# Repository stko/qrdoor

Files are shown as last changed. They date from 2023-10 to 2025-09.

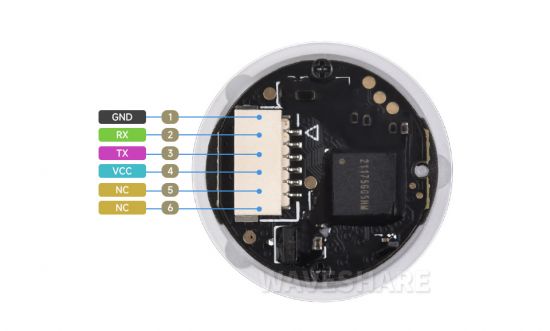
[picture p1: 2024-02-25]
circuit/pico/Barcode_module_b05.jpg

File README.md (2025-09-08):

# QRDoor - A QRCode Reader & MQTT Door Opener

Even as made as add-on for the [Zuul Acess Control System](https://github.com/stko/zuul-ac), it's also suitable whereever a MQTT driven QR code reader and door opener output is needed.

## What it does
* it quickly reads all codes which are presented to the camera
* the read codes are sent as a mqtt message
* it waits for incoming mqtt messages to activate the output pin (to control a door opener)
* as a convinience function, it monitors an input pin (as door bell button) and reports its state change via mqtt

## Setup
For the hardware connect your rpi pico as shown in the circuit/qrcode_pico schematic.

For the software installion the Thonny IDE was used. The steps are
* for micropython follow the instructions on https://micropython.org/download/RPI_PICO_W/. Make sure you install the version for the *WIFI version* of the Rasperry Pico!
* connect your Thonny IDE with your pico device
* In Thonny, in "Tools/Manage Packages.." install the both packages umqtt.simple2 and umqtt.robust2 (MAKE SURE YOU GOT THE ....2 VERSION)
* copy the provided file `settings_template.json`to `settings.json`
* edit the new file `settings.json` and set your own settings
* via Thonny, copy both main.py and settings.json onto your pico device
* run the program

## Operation
* at start qrdoor tries to connect with the given WIFI. This loop is repeated until the connection is made.
* then it waits for either for a scanned code, a button press or an open command

## MQTT commands
### Scanned code
When a code is read, its published to `qrdoor/<device- id>/code`
  
### Button Press
When the button is pressed or released, the state is reported to `qrdoor/<device- id>/button` as `on` or `off`

### Door Open command
When the `qrdoor/<device- id>/open` \<secs\> topic is received, both LED and output pins are set to High for \<secs\> seconds. To avoid unwanted longer power output, this time is limited to 5 secs.

## Setup
Depending on the factory setting of a fresh GM60 qr code reader out of the box, it might be that the qr code reader does not send a trailing <CR> after each scan, which is needed by the software to identify the end of the scan. To fix this, there are configuration QR Codes in the GM60 user manual. Just scan the one named "Add tail 'CR'" to set the trailing <CR>.

## History
Originally the whole project was started to use a ESP32CAM module for it. This work can be found in the qrdoor folder as an Arduino Project. It finally worked in some way, but it came out that the ESPCAM can't handle it properly when suddenly a mobile phone with a qrcode on it is presented to the camera. All the brightness control and auto focus need to be completely re- adjusted, which takes at least 10 seconds, and during the whole time the user needs to hold the mobile phone stable and calm in a constant position and distance in front to the camera - and this just don't work.

So finally the whole project was restarted, this time with a Raspberry Pico, Micropython and the ready-to-go QR-Code Reader from Waveshare (which seems to be a GROW GM861, which can be ordered in Asia). With that it just took a relaxed weekend to get it to work, mainly because of the very well working barcode reader.

## Links

Micropython Image *with* WLAN - Support:  https://micropython.org/download/rp2-pico-w/rp2-pico-w-latest.uf2
The QR Reader Module: https://www.waveshare.com/wiki/Barcode_Scanner_Module_(D)
which is a GROW GM60 module

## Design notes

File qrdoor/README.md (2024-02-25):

# QRDoor - Scans QRCodes via ESP32-CAM and send them via MQTT

(not fully finalized, QR is working, the additional IOs are not implemented yet)

QRDoor is a generic application to read QRCodes with a ESP32-CAM module and forward them via MQTT.

It also supports, controlled by MQTT :
- one Input (e.g. for adoor bell button)
- one triggered output port (for the door lock)

All the Wifi setup is made through the [WifiMQTTManager](https://github.com/dreed47/WifiMQTTManager/tree/master#access-point-configuration), which provides an easy to use setup hotspot.

## Limitations
Please be aware that the combination of cheap processor and low-cost camera is far behind the performance of a Desktop PC with a high speed & resolution webcam. What does that mean in detail?:
* The standard lens together with the auto focus allows only a small distance range where the qrcode can be placed (~25 cm). If it is too far, the qrcode becomes too small, but if it is too close, the picture becomes blurry
* The autofocus and the brightness control is very slow, and each picture change triggers a re-adjustment

Because of that it's quite impossible to just hold a mobile phone free hand anywhere in front of the camera. The movements of the hand are much quicker as the autofocus :-(

So to read a qrcode from any surface or from a phone, it's highly recommended to construct something like a filing for the object carrying the qrcode in front of the camera to keep the object in position so that the camera can generate a stable picture.

Also the user needs to be made aware that the recognition process can easily take 10 seconds...

## Hardware

Just as a starting point the io pins have been taken from [here](https://www.electroniclinic.com/esp32-cam-smart-iot-bell-circuit-diagram-and-programming/) and put into a KiCad schematic separated into two sections:
* one pcb close to the bell transformator containing the DC converter and the door opener output
* a second pcb carrying the ESP32cam and its voltage converter

Schematic

## Setup

The development was made with the VSCode Arduino Extention, so the setup for the original Arduino IDE should be very simular.

1) First add (if not already done) the URL for the Espressif Board in "Board Manager / Addional URLs":“[https://dl.espressif.com/dl/package_esp32_index.json”](https://dl.espressif.com/dl/package_esp32_index.json%E2%80%9D)

2) In the Board Manager, search for "esp32" and install "Esp32 from Espressif Systems”
3) Select the right board: “ESP32 Wrover"
4) In the Library Manager, install several Libraries. Here's the output from the todays build log:

```
Used library            Version     Pfad                                                                             
WiFiMQTTManager Library 1.0.1-beta   
WiFiManager             2.0.15-rc.1            
WiFi                    2.0.0
Update                  2.0.0
WebServer               2.0.0
DNSServer               2.0.0
ArduinoJson             5.13.5
PubSubClient            2.8
FS                      2.0.0
SPIFFS                  2.0.0
```
Make sure the Arduino Json Library  is a **5.xx** version!!

In Tools-Board select :
- ESP32Wrover Module
- Speed 921600
- Flash Frequency 80Mhz
- Flash Mode QIO
- Partition Scheme: Huge app

## Hacks

After installing WiFiMQTTManager, go into the library file `.../WiFiMQTTManager.cpp` and move the `Serial.begin(115200);`line as the first line of the constructor

```WiFiMQTTManager::WiFiMQTTManager(int resetPin, char* APpassword) {
  Serial.begin(115200);
  wm = new WiFiManager;
  lastMsg = 0;
  formatFS = false;
  ```

add the line `client->setBufferSize(512);` after the `client.reset(new PubSubClient(_espClient));`

```
  client.reset(new PubSubClient(_espClient));
  client->setBufferSize(512);
  client->setServer(_mqtt_server, port);
  ```

comment out the line 158 `wm->resetSettings();` to not loose all settings after failed MQTT server attempt.. and modify delay timings

```
  client->setServer(_mqtt_server, port);
  delay(2000);
  Serial.print("WMM: attempting MQTT connection...");
  if (!client->connect(clientId)) {
    Serial.println("failed to connect to MQTT -wait 10 secs and restart...");
    delay(10000);
//    wm->resetSettings();
    ESP.restart(); 
```

Modify the `SPIFFS.begin()` line from

` if (SPIFFS.begin()) {`

to 

 `if (SPIFFS.begin(false) || SPIFFS.begin(true)){ `

to format the filesystem at the inital start

in \~/snap/arduino/85/.arduino15/packages/esp32/hardware/esp32/1.0.6/cores/esp32/main.cpp

increase the task stack size

```cpp
#ifndef CONFIG_ARDUINO_LOOP_STACK_SIZE
#define CONFIG_ARDUINO_LOOP_STACK_SIZE 8192
#endif

//// ---- ADD this -----
#define CONFIG_ARDUINO_LOOP_STACK_SIZE 32768
```

## Credits

- The program skeleton comes from the  WiFiMQTTManager demo code

- The image capture routines are from [GitHub - donny681/ESP32_CAMERA_QR](https://github.com/donny681/ESP32_CAMERA_QR)

-  The qrcode detection routines are from [GitHub - dlbeer/quirc: QR decoder library](https://github.com/dlbeer/quirc)
and

- qrcode code sample [GitHub - donny681/ESP32_CAMERA_QR](https://github.com/donny681/ESP32_CAMERA_QR)

Detailed Info about the ESP32CAM: https://lastminuteengineers.com/getting-started-with-esp32-cam/

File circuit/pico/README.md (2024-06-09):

# Details

## Pico Pinout

top view, QRCode reader on the left, Power on the right

| Left | Right |
| --- | ----- |
| BL | |
| OR | |
| BR | |
| GR | |
| (Relay) | GN |
| (GND) | WH |
| (V+) | RT |

## Power supply

| Meaning | (color) |
| --- | --- |
| AC/DC 1 | |
| AC/DC 2 | |
| Door Opener 1 | |
| Door Opener 2 | |
| V+ | RT |
| GND | WH |
| Relay | GN |

## QRCode- Reader Pinout

GND: Ground
RX: UART input pin
TX: UART output pin
VCC: 3.3V power supply
NC: Reserved, not connected
NC: Reserved, not connected

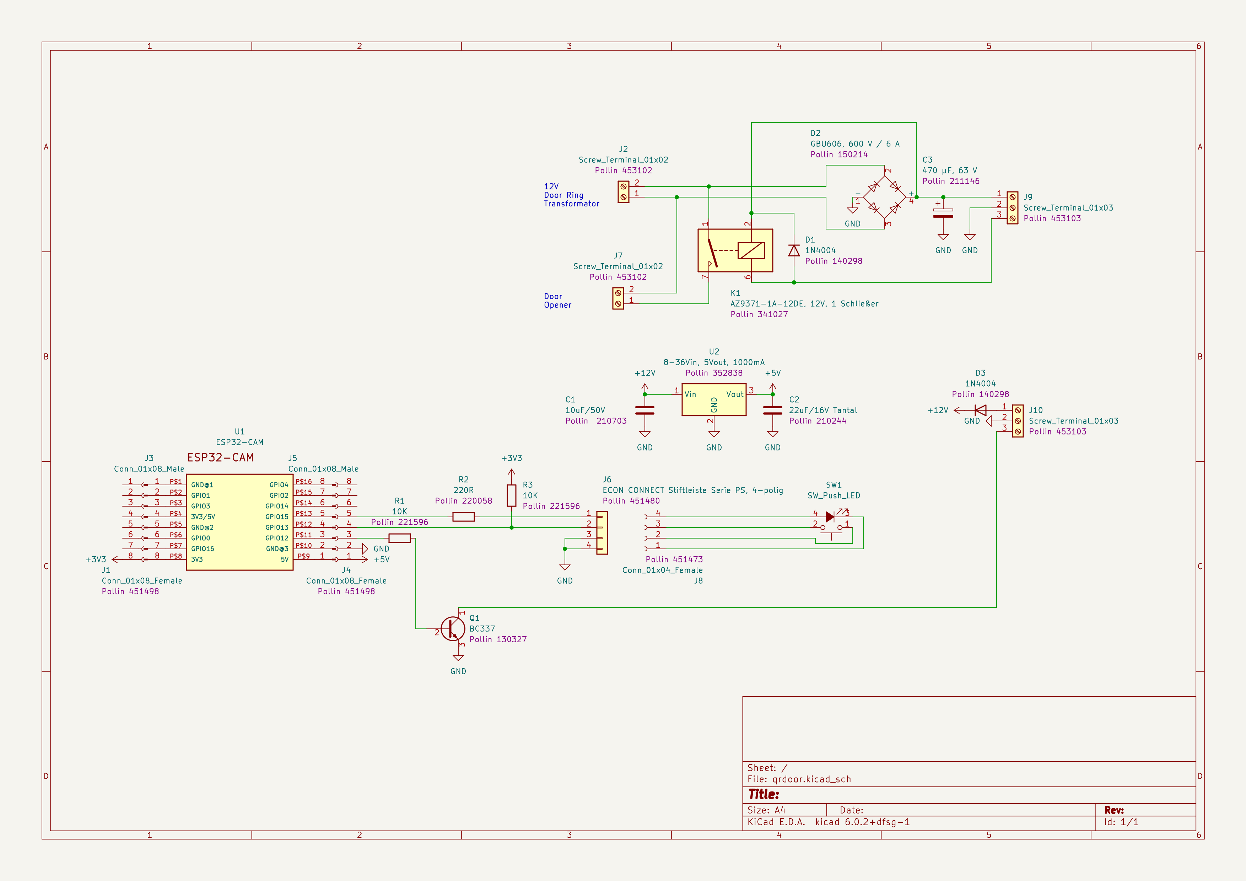
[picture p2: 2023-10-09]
images/schematig.png

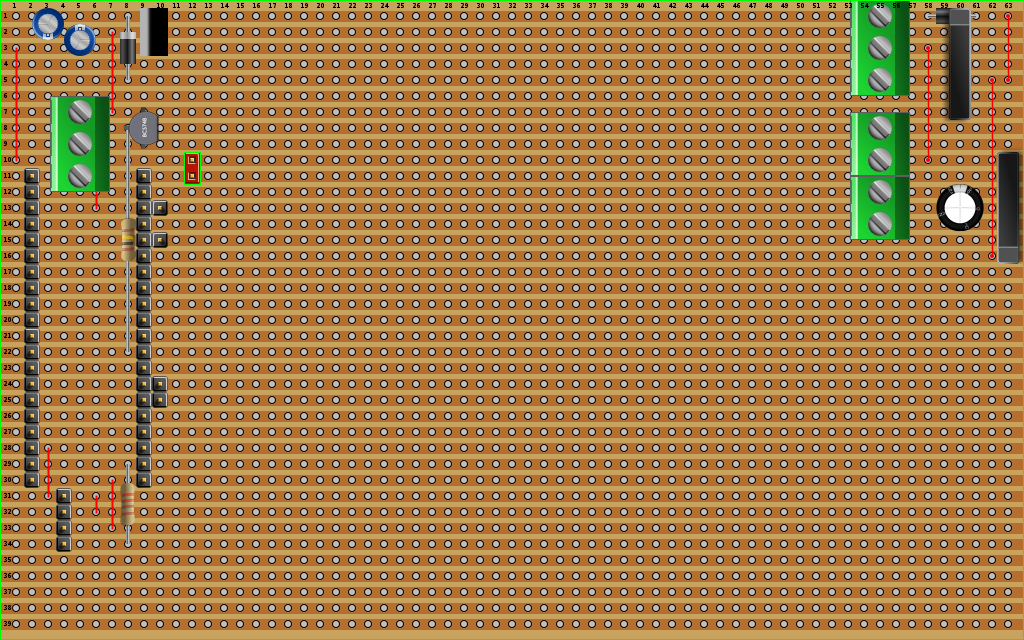
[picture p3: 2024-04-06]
circuit/pico/pcb_cheap.png

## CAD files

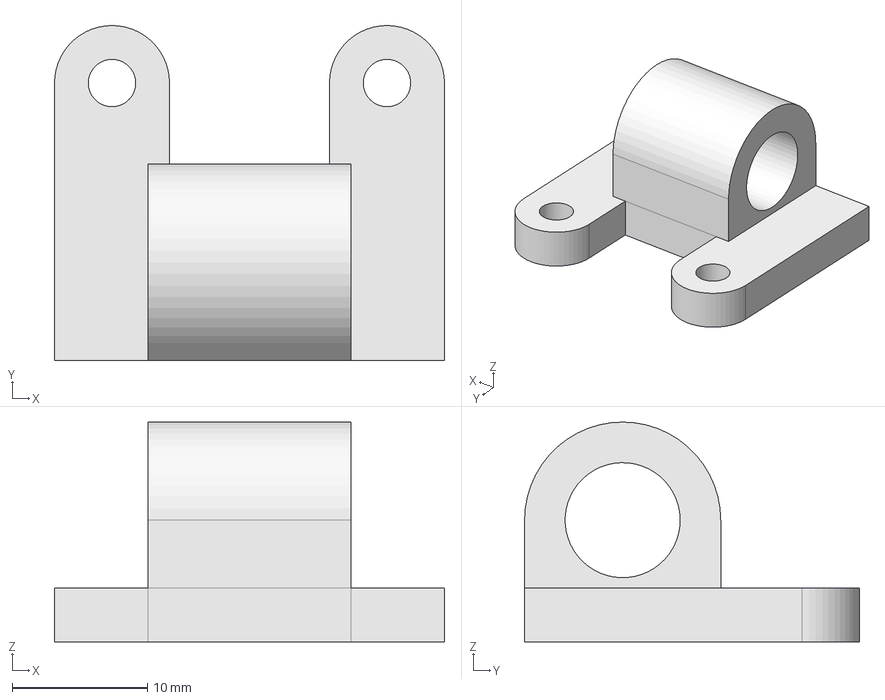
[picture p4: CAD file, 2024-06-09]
cad/pcb_holder_small.FCStd
28.8 x 24.8 x 16.3 mm

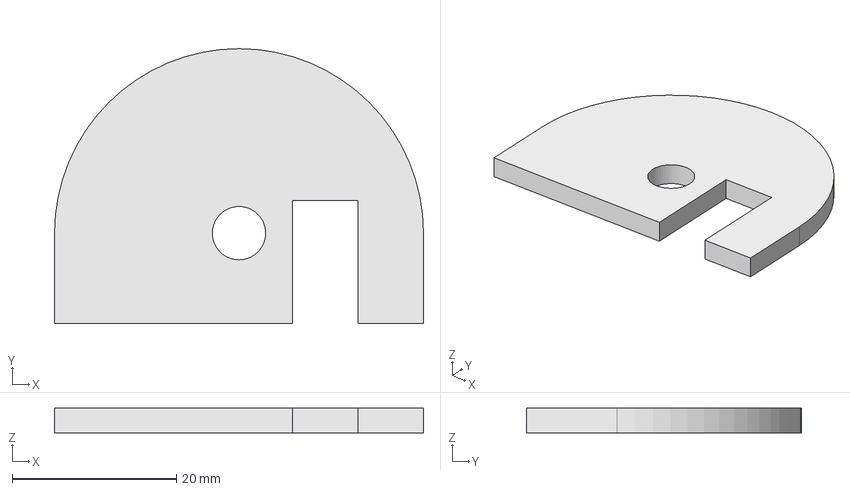
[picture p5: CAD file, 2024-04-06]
cad/front_plate_2_M6.FCStd
45.0 x 33.5 x 3.00 mm

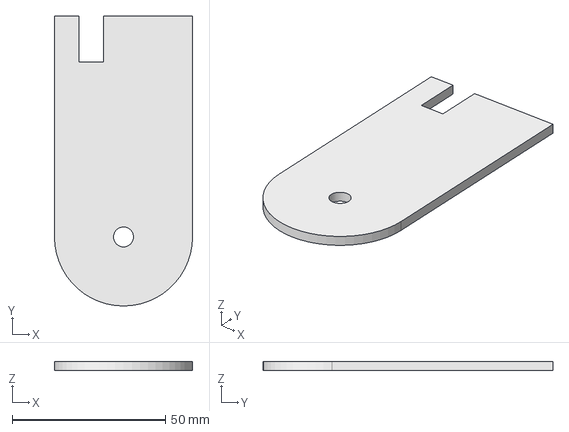
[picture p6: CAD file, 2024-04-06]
cad/front_plate_3_M6.FCStd
45.0 x 94.5 x 3.00 mm

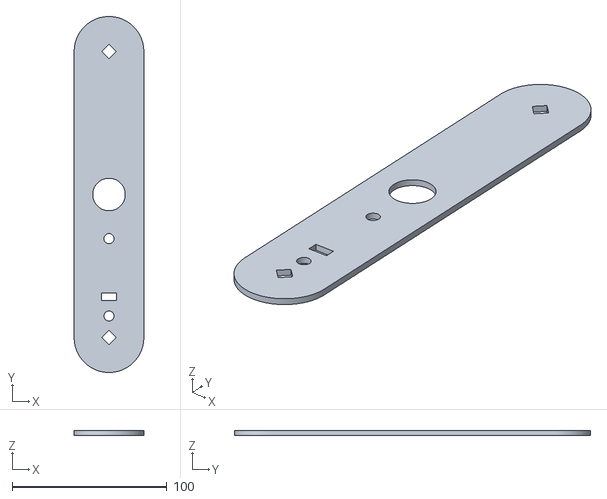
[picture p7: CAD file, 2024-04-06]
cad/front_plate_M6-Körper.stl
45.0 x 230.0 x 3.00

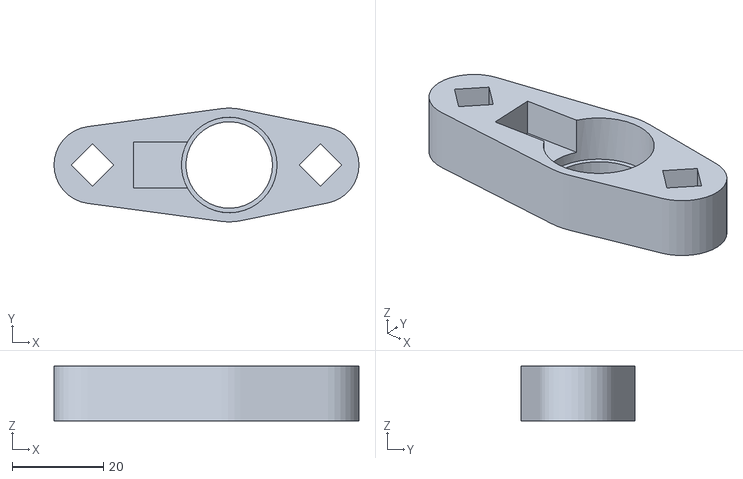
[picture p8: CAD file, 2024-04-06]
cad/camera_cover_M6-Körper.stl
67.0 x 25.0 x 12.0

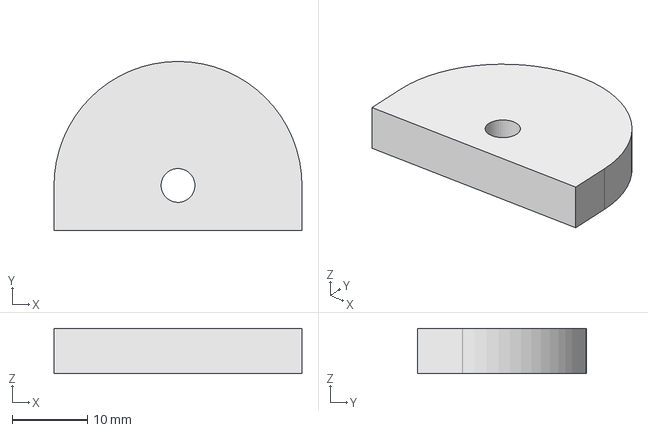
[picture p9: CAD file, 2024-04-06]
cad/distance_plate.FCStd
33.0 x 22.5 x 6.00 mm

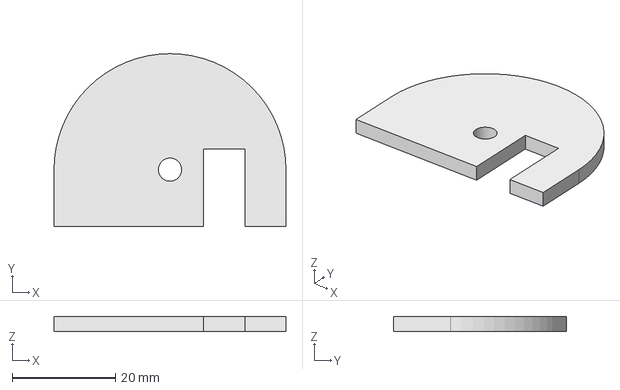
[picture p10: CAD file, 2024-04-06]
cad/front_plate_2.FCStd
45.0 x 33.5 x 3.00 mm

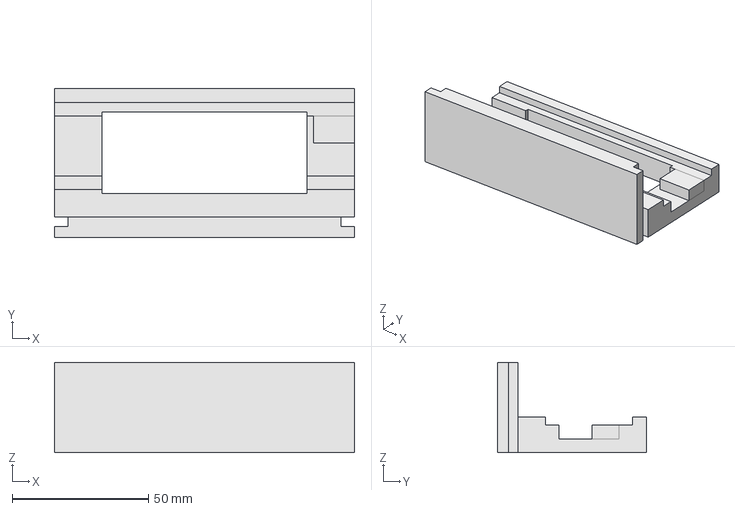
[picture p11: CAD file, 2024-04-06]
cad/pcb_holder.FCStd
110.0 x 54.5 x 33.0 mm

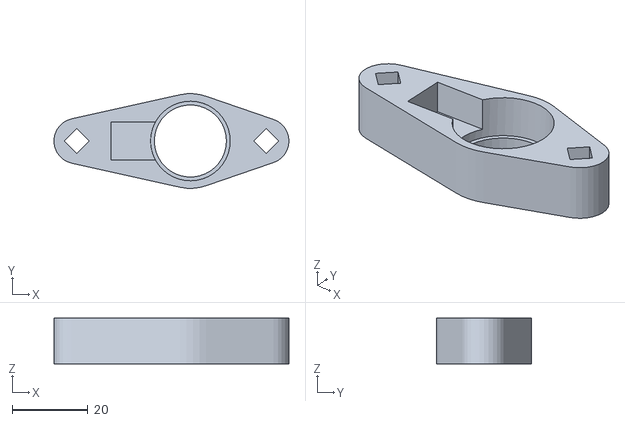
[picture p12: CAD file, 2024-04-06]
cad/camera_cover-Körper.stl
62.0 x 25.0 x 12.0

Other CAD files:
cad/front_plate_2_M6-Körper.stl
cad/pcb_holder-Körper.stl
cad/camera_cover_M6.FCStd
cad/front_plate.FCStd
cad/distance_plate_M6.FCStd
cad/front_plate_3.FCStd
cad/distance_plate_M6-Körper.stl
cad/distance_plate-Körper.stl
cad/front_plate_M6.FCStd
cad/camera_cover.FCStd
cad/front_plate_3_M6-Körper.stl

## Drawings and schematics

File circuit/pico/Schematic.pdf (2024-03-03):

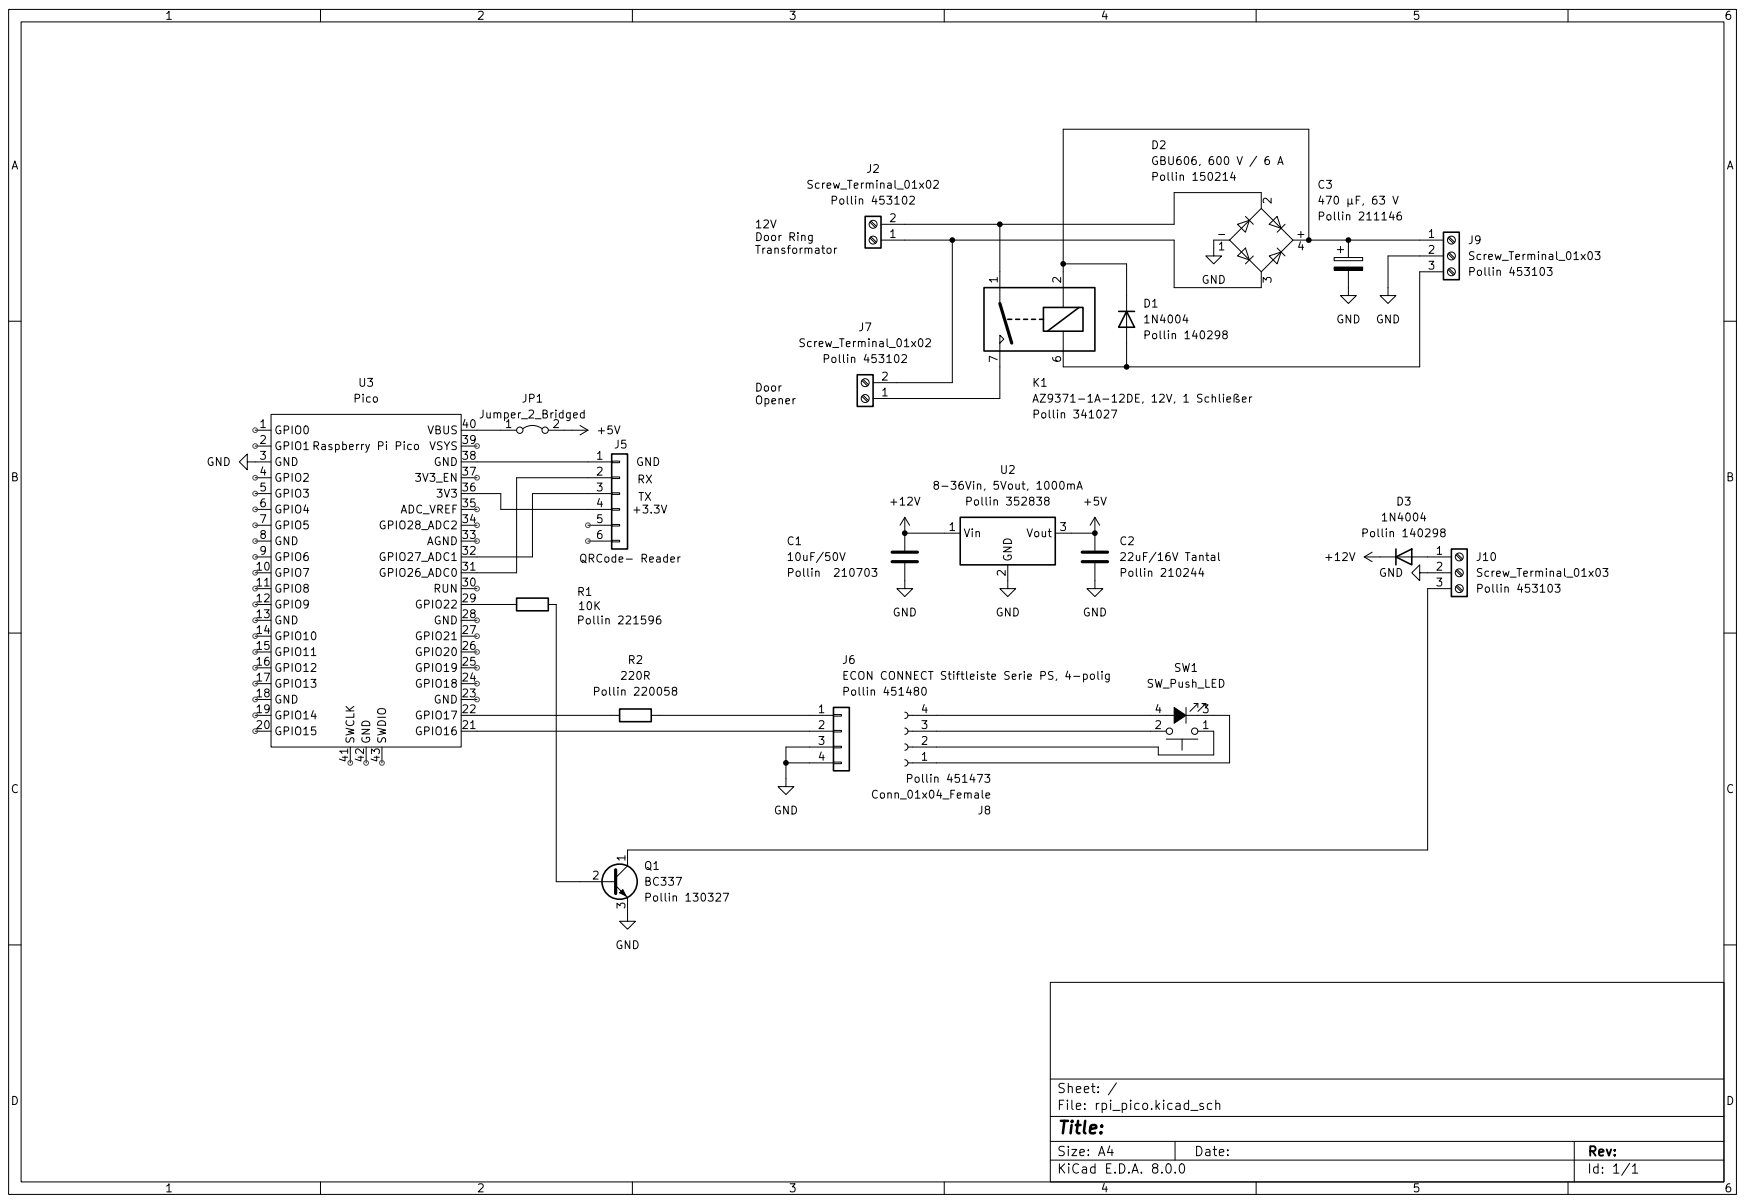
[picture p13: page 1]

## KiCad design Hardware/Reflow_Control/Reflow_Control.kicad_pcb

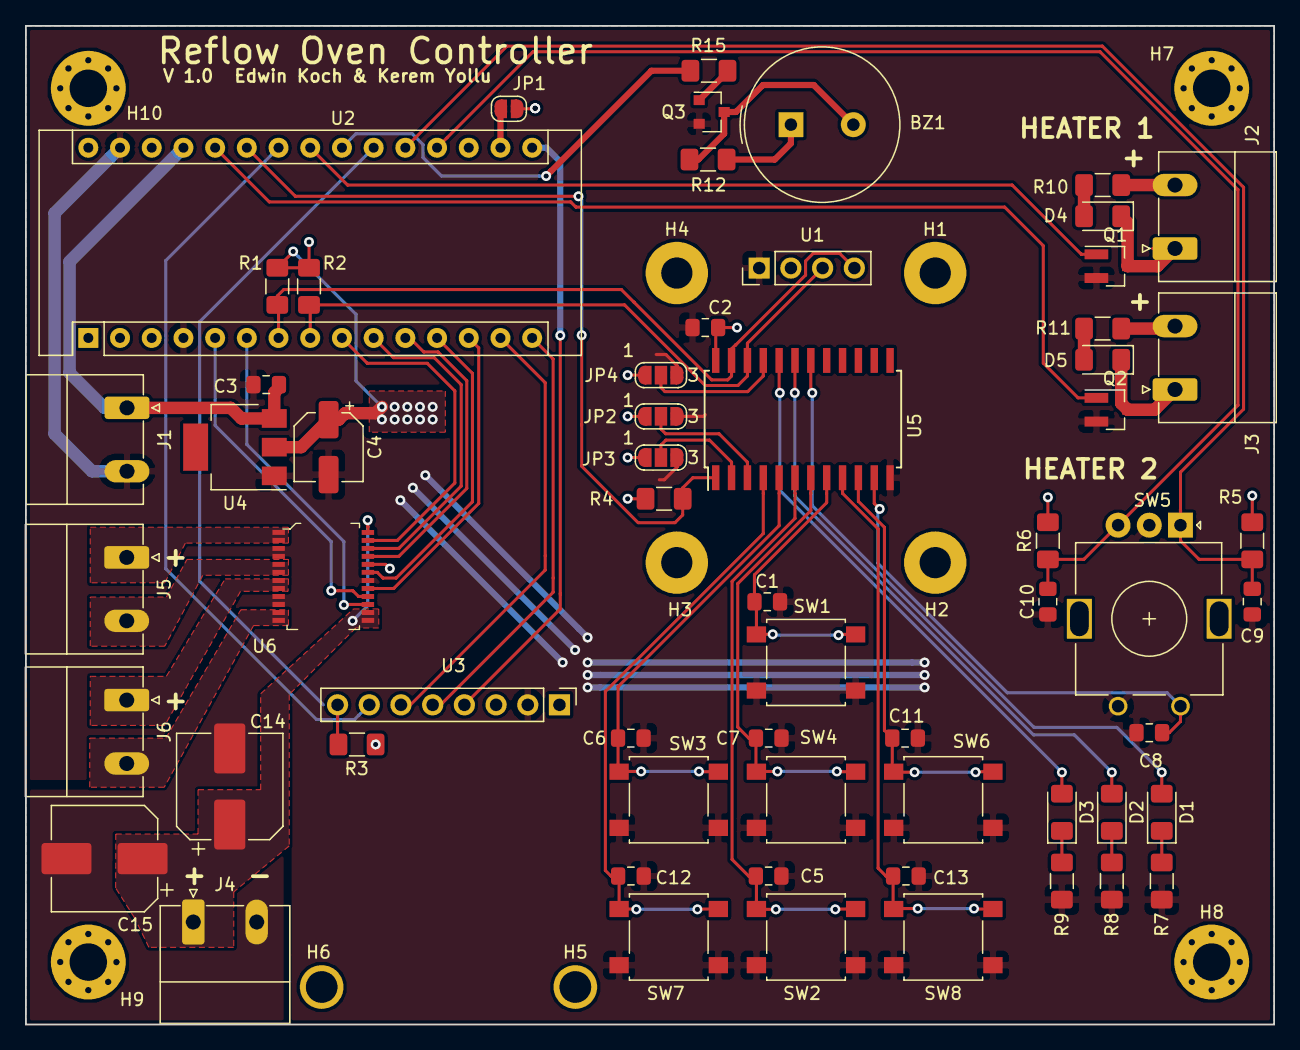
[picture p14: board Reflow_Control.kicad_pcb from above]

Board: 2 copper layers, 100.0 x 80.0 mm, 71 parts (0 on the bottom side), 52 nets.

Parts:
BZ1: Buzzer; Buzzer_TDK_PS1240P02BT_D12.2mm_H6.5mm
C1, C3, C5, C6, C7, C8, C9, C10, C11, C12, C13: 10uF; C_0805_2012Metric_Pad1.15x1.40mm_HandSolder
C2: 100n; C_0805_2012Metric_Pad1.15x1.40mm_HandSolder
C4: 100uF; CP_Elec_5x5.4
C14, C15: 100uF; CP_Elec_8x6.2
D1, D2, D3, D4, D5: LED; LED_1206_3216Metric_Pad1.42x1.75mm_HandSolder
H1, H2, H3, H4, H5, H6: MountingHole; MountingHole_2.5mm_Pad
H7, H8, H9, H10: MountingHole; MountingHole_3mm_Pad_Via
J1: Conn_5V; PhoenixContact_MC_1,5_2-G-5.08_1x02_P5.08mm_Horizontal
J2: Conn_ssr_1; PhoenixContact_MC_1,5_2-G-5.08_1x02_P5.08mm_Horizontal
J3: Conn_ssr_2; PhoenixContact_MC_1,5_2-G-5.08_1x02_P5.08mm_Horizontal
J4: Conn_mot_PWR; PhoenixContact_MC_1,5_2-G-5.08_1x02_P5.08mm_Horizontal
J5: Conn_mot_1; PhoenixContact_MC_1,5_2-G-5.08_1x02_P5.08mm_Horizontal
J6: Conn_mot_2; PhoenixContact_MC_1,5_2-G-5.08_1x02_P5.08mm_Horizontal
JP1: 3.3V Jumper; SolderJumper-2_P1.3mm_Open_RoundedPad1.0x1.5mm
JP2, JP3, JP4: ADDR_A2; SolderJumper-3_P1.3mm_Open_RoundedPad1.0x1.5mm_NumberLabels
Q1: Q_NMOS_GSD; SOT-23_Handsoldering
Q2: NUD3112LT1G; SOT-23_Handsoldering
Q3: BC848; SOT-23
R1, R2, R3, R4, R5, R6, R7, R8, R9: 4k7; R_1206_3216Metric_Pad1.42x1.75mm_HandSolder
R10, R11, R12, R15: 1k; R_1206_3216Metric_Pad1.42x1.75mm_HandSolder
SW1, SW2, SW3, SW4, SW6, SW7, SW8: SW_Push; SW_SPST_B3S-1000
SW5: Rotary_Encoder_Switch; RotaryEncoder_Alps_EC11E_Vertical_H20mm
U1: SSD1306_128x64; PinHeader_1x04_P2.54mm_Vertical
U2: NUCLEO-F042K6; Arduino_Nano
U3: MAX31865_Breakout; PinHeader_1x08_P2.54mm_Vertical
U4: LM1117-3.3; SOT-223
U5: PCA9555; SOIC-24W_7.5x15.4mm_P1.27mm
U6: TB6612FNG_C_8_EL; LSSOP-24_W5.6mm

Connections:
+3V3: BZ1.1, C2.2, C4.1, J2.2, J3.2, JP1.2, JP2.1, JP3.1, JP4.1, R1.1, R2.1, R3.1, R4.1, R5.1, R6.1, R10.1, R11.1, R12.1, U1.2, U3.3, U4.2, U5.24, U6.20
+5V: C3.1, J1.1, U2.27, U4.3
/motor_vcc: C14.1, C15.1, J4.1, U6.13, U6.14, U6.24
ADDR_A0: JP4.2, U5.21
ADDR_A1: JP3.2, U5.2
ADDR_A2: JP2.2, U5.3
BTN_A: C12.1, SW7.1, U5.4
BTN_B: C13.1, SW8.1, U5.9
BTN_CENTER: C7.1, SW4.1, U5.7
BTN_DOWN: C5.1, SW2.1, U5.6
BTN_LEFT: C6.1, SW3.1, U5.5
BTN_RIGHT: C11.1, SW6.1, U5.10
BTN_UP: C1.1, SW1.1, U5.8
CH1_MOTOR_IN1: U2.11, U6.21
CH1_MOTOR_IN2: U2.10, U6.22
CH1_MOTOR_STBY: U2.12, U6.19
CH2_MOTOR_IN1: U2.5, U6.16
CH2_MOTOR_IN2: U2.13, U6.17
ENC_Switch: C8.2, SW5.S1, U5.11
GND: C1.2, C2.1, C3.2, C4.2, C5.2, C6.2, C7.2, C8.1, C9.1, C10.1, C11.2, C12.2, C13.2, C14.2, C15.2, J1.2, J4.2, JP2.3, JP3.3, JP4.3, Q1.2, Q2.2, Q3.2, R7.2, R8.2, R9.2, SW1.2, SW2.2, SW3.2, SW4.2, SW5.C, SW5.S2, SW6.2, SW7.2, SW8.2, U1.1, U2.4, U2.29, U3.2, U4.1, U5.12, U6.3, U6.4, U6.9, U6.10, U6.18
I2C1_SCL: R2.2, U1.3, U2.8, U5.22
I2C1_SDA: R1.2, U1.4, U2.7, U5.23
INT_ENC_A: C10.2, R6.2, SW5.B, U2.19
INT_ENC_B: C9.2, R5.2, SW5.A, U2.20
INT_MAX31865_RDY: R3.2, U2.21, U3.8
INT_PCA9555: R4.2, U2.25, U5.1
unnamed: BZ1.2, Q3.3, R12.2
unnamed: D1.1, R7.1
unnamed: D1.2, U5.18
unnamed: D2.1, R8.1
unnamed: D2.2, U5.19
unnamed: D3.1, R9.1
unnamed: D3.2, U5.20
unnamed: D4.1, J2.1, Q1.3
unnamed: D4.2, R10.2
unnamed: D5.1, J3.1, Q2.3
unnamed: D5.2, R11.2
unnamed: J5.1, U6.1, U6.2
unnamed: J5.2, U6.5, U6.6
unnamed: J6.1, U6.7, U6.8
unnamed: J6.2, U6.11, U6.12
unnamed: JP1.1, U2.17
unnamed: Q3.1, R15.1
SPI1_CS_MAX31865: U2.24, U3.7
SPI1_MISO: U2.15, U3.5
SPI1_MOSI: U2.14, U3.6
SPI1_SCK: U2.16, U3.4
SSR_1: Q1.1, U2.23
SSR_2: Q2.1, U2.26
TIM1_CH1_PWM_Buzzer: R15.2, U2.22
TIM3_CH1_MOTOR_PWM: U2.9, U6.23
TIM3_CH2_MOTOR_PWM: U2.6, U6.15

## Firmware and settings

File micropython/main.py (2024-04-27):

# Bibliotheken laden
from machine import UART, Pin, unique_id, reset
import sys
import network
from umqtt.robust2 import MQTTClient
import utime
import ujson
import time

def connectMQTT(device_id):
    """
    does all the MQTT setup
    """
    client = MQTTClient(
        client_id=b"QRDOOR_" + device_id,
        server=settings["mqtt_server"].encode("utf-8"),
        port=settings["mqtt_port"],
        user=settings["mqtt_user"].encode("utf-8"),
        password=settings["mqtt_password"].encode("utf-8"),
        keepalive=settings["mqtt_keepalive"],
        ssl=settings["mqtt_ssl"],
        ssl_params=settings["mqtt_serial_params"],
    )
    client.connect()
    client.set_callback(subscribe)
    topic = "qrdoor/" + device_id + "/#"
    client.subscribe(topic)
    print("subscribe to topic", topic)
    return client

def subscribe(topic, msg, retain, dup ):
    '''
    handle the received topic
    '''

    global device_id, last_watchdog_rcv
    topic = topic.decode("utf-8")
    msg = msg.decode("utf-8")
    print("topic", topic, msg)
    last_watchdog_rcv=time.time()
    if topic == "qrdoor/" + device_id + "/open":
        try:
            seconds = int(msg)
            if seconds < 6 and seconds > 0:
                set_relais(seconds)
        except:
            pass
    if topic == "qrdoor/" + device_id + "/reset":
        print("MQTT Remote Reboot")
        reset() # brute force error handling..

def set_relais(seconds):
    '''
    turns on the both output for indicator led and relais output for given seconds, if less 6 secs to avoid permanent power output
    '''
    global output_switch_time_ticks, relais, led
    output_switch_time_ticks = utime.ticks_add(utime.ticks_ms(), seconds * 1000)
    relais_pin.value(1)
    led_pin.value(1)
    print("ON for relay and LED")


def control_relais():
    '''
    checks the on time and switches off again when time is reached
    '''
    global output_switch_time_ticks, relais, led
    if (
        output_switch_time_ticks > 0
        and utime.ticks_diff(output_switch_time_ticks, utime.ticks_ms()) > 0
    ):
        return
    if output_switch_time_ticks > 0:
        relais_pin.value(0)
        led_pin.value(0)
        output_switch_time_ticks = 0
        print("OFF for relay and LED")


# reads the settings file
try:
    with open("settings.json", encoding="utf-8") as fin:
        settings = ujson.load(fin)
        print("settings loaded from file")
except:
    print("No settings found, using defaults")
    settings = {
        "wlan_ssid": "ssid",
        "wlan_password": "wifi_password",
        "mqtt_server": "mqtt_server",
        "mqtt_port": 0,
        "mqtt_user": "mqtt_user",
        "mqtt_password": "mqtt_password",
        "mqtt_keepalive": 7200,
        "mqtt_ssl": False,
        "mqtt_serial_params": {},
    }

relais_pin = Pin(22, Pin.OUT)
led_pin = Pin(17, Pin.OUT)
switch_pin = Pin(16, Pin.IN, pull=Pin.PULL_UP)
rx_pin=Pin(21)
tx_pin=Pin(20)
uart_id=1

output_switch_time_ticks = 0

# calculate the device id
s = unique_id()
device_id = ""
for b in s:
    device_id += hex(b)[2:]


# UART0 initialization
uart = UART(uart_id, baudrate=9600, tx=tx_pin, rx=rx_pin, bits=8, parity=None, stop=1)
print("UART:", uart)

wlan = network.WLAN(network.STA_IF)
wlan.active(True)
wlan.config(pm=0xA11140)  # Diable powersave mode
print(settings["wlan_ssid"], settings["wlan_password"])
wlan.connect(settings["wlan_ssid"], settings["wlan_password"])


# Note that this may take some time, so we need to wait
# Wait 5 sec or until connected
tmo = 50
while not wlan.isconnected():
    utime.sleep_ms(100)
    led_pin.toggle()
    tmo -= 1
    if tmo == 0:
        break

# check if the station is connected to an AP
if wlan.isconnected():
    print("=== Station Connected to WiFi \n")
    config = wlan.ifconfig()
    led_pin.value(0)
    print("IP:{0}, Network mask:{1}, Router:{2}, DNS: {3}".format(*config))
else:
    print("wifi connection failed")
    utime.sleep(10)
    led_pin.value(1)
    reset()


client = connectMQTT(device_id)

# uart input buffer
line = ""

last_switch_state = False
watchdog_interval= 6 # defines the time between two watchdog messages
watchdog_nr_of_fails = 3 # defines the trigger level, how many times a message can fail before the system resets
last_watchdog_rcv=time.time()
last_watchdog_send=0
try:
    client.publish("qrdoor/" + device_id + "/start", "1")
    while True:
        actual_time_secs=time.time()
        # read the switch
        switch_state = switch_pin.value() != 1
        if switch_state and not last_switch_state:  # raising switch event
            last_switch_state = True
            client.publish("qrdoor/" + device_id + "/button", "on")
            print("button raising edge")
        if not switch_state and last_switch_state:  # raising switch event
            client.publish("qrdoor/" + device_id + "/button", "off")
            print("button falling edge")
        last_switch_state = switch_state
        # print("switch", switch_state)
        if last_watchdog_send + watchdog_interval <= actual_time_secs:
            client.publish("qrdoor/" + device_id + "/watchdog", str(actual_time_secs))
            last_watchdog_send = actual_time_secs
        if last_watchdog_rcv + watchdog_nr_of_fails * watchdog_interval < actual_time_secs:
            print("Watchdog trigger, Reboot: ")
            reset() # brute force error handling..
        control_relais()
        client.check_msg()
        rxData = uart.readline()
        if rxData:
            print("bin",rxData)
            rxData = rxData.decode("utf-8")
            print("as str\"",rxData,"\"")
            rxChars=rxData
            line += rxChars.strip() ##add wthout eol
            print("linebuffer",line)
            if rxData[-1:]== "\r": # the QRCode reader sent
                print(line)
                # publish as MQTT payload
                client.publish("qrdoor/" + device_id + "/code", line)
                line = ""

                
except Exception as ex:
    text=str(ex)
    print("System Error, Reboot: ",text)
    reset() # brute force error handling..

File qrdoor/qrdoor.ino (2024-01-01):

/*
 * wifiMQTTManager from https://github.com/dreed47/WifiMQTTManager/blob/master/examples/Basic/Basic.ino
 * Required Libraries
 * WiFiManager Library
 * Arduino Json Library 5.xx !!
 * PubSub Client Library
 *     NOTE: Read README.md of how to tweak the library!!
 * 
 * Hardware connections (inspired from https://www.electroniclinic.com/esp32-cam-smart-iot-bell-circuit-diagram-and-programming/)
 * 
 * Pin 1 : 5V
 * Pin 2 : GND
 * Pin 3 : Door lock relay driver output 3.3V High active (GPIO 12)
 * Pin 4 : Door bell button switch to gnd (GPIO 13)
 * Pin 5 : Indicator LED output High active (GPIO 15)
 *
 */

#include <string.h>

#if !defined ESP32
#error This sketch is only for an ESP32Cam module
#endif

#include "qrtask.h"

#include "config.h"

#include "WiFiMQTTManager.h"
#include "PubSubClient.h"

// ##########  Settings ########
const int TimeBetweenStatus = 600; // speed of flashing system running ok status light (milliseconds)
const int indicatorLED = 33;       // onboard small LED pin (33)

// #define LED_PIN 4
#define LED_PIN indicatorLED

// Button that will put device into Access Point mode to allow for re-entering WiFi and MQTT settings
#define RESET_BUTTON 3

uint32_t lastStatus = millis(); // last time status light changed status (to flash all ok led)

extern QueueHandle_t xQrCodeQueue;
extern WiFiManager *wm;

WiFiMQTTManager wmm(RESET_BUTTON, AP_PASSWORD); // AP_PASSWORD is defined in the secrets.h file

TaskHandle_t QrReaderTask;

void setup()
{
  pinMode(LED_PIN, OUTPUT);
  Serial.begin(115200);
  Serial.setDebugOutput(true);
  Serial.println();
  // Serial.println(F("WiFiMQTTManager Basic Example"));
  Serial.println("WiFiMQTTManager Basic Example");

  // set debug to true to get verbose logging
  wm->setDebugOutput(true);
  wm->setConnectTimeout(5);
  // most likely need to format FS but only on first use
  // wmm.formatFS = true;
  // optional - define the function that will subscribe to topics if needed
  wmm.subscribeTo = subscribeTo;
  // required - allow WiFiMQTTManager to do it's setup
  wmm.setup(__SKETCH_NAME__);
  // optional - define a callback to handle incoming messages from MQTT
  wmm.client->setCallback(subscriptionCallback);

  // Set up Core 1 task handler

  /* Create a queue capable of containing 10 pointers to qrcode string.  These are to be queued by pointers as they are
  relatively large structures. */
  xQrCodeQueue = xQueueCreate(10, sizeof(char *));

  if (xQrCodeQueue != NULL)
  {

    // xTaskCreate(qrtask, "qrtask", 32768, NULL, 1, NULL);
    xTaskCreatePinnedToCore(
        qrtask,
        "qrtask",
        32768,
        (void *)xQrCodeQueue,
        1,
        &QrReaderTask,
        1);
  }
}

void loop()
{
  // delay(500);
  // digitalWrite(LED_PIN, !digitalRead(LED_PIN));
  //  Serial.println("Wloop");
  //   required - allow WiFiMQTTManager to check for new MQTT messages,
  //   check for reset button push, and reconnect to MQTT if necessary
  wmm.loop();
  char *qrCodeStr;
  while (xQueueReceive(xQrCodeQueue,
                       &qrCodeStr,
                       (TickType_t)0) == pdPASS)
  {
    Serial.print("received QR: ");
    Serial.println(qrCodeStr);
    char topic[100];
    snprintf(topic, sizeof(topic), "%s%s%s", "qrdoor/", wmm.deviceId, "/qrcode");
    wmm.client->publish(topic, qrCodeStr, true);
    free(qrCodeStr);
  }

  // optional - example of publishing to MQTT a sensor reading once a 1 minute
  long now = millis();
  if (now - wmm.lastMsg > 60000)
  {
    wmm.lastMsg = now;
    float temperature = 70; // read sensor here
    Serial.print("Temperature: ");
    Serial.println(temperature);
    char topic[100];
    snprintf(topic, sizeof(topic), "%s%s%s", "sensor/", wmm.deviceId, "/temperature");
    wmm.client->publish(topic, String(temperature).c_str(), true);
  }
  // flash status LED to show sketch is running ok
  if ((unsigned long)(millis() - lastStatus) >= TimeBetweenStatus)
  {
    lastStatus = millis();                                  // reset timer
    digitalWrite(indicatorLED, !digitalRead(indicatorLED)); // flip indicator led status
  }
}

// optional function to subscribe to MQTT topics
void subscribeTo()
{
  Serial.println("subscribing to some topics...");
  // subscribe to some topic(s)
  char topic[100];
  snprintf(topic, sizeof(topic), "%s%s%s", "switch/", wmm.deviceId, "/led1/output");
  wmm.client->subscribe(topic);
}

// optional function to process MQTT subscribed to topics coming in
void subscriptionCallback(char *topic, byte *message, unsigned int length)
{
  Serial.print("Message arrived on topic: ");
  Serial.print(topic);
  Serial.print(". Message: ");
  String messageTemp;

  for (int i = 0; i < length; i++)
  {
    Serial.print((char)message[i]);
    messageTemp += (char)message[i];
  }
  Serial.println();

  // if (String(topic) == "switch/esp1234/led1/output") {
  //   Serial.print("Changing led1 output to ");
  // }
}

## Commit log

2023-02-05 reads QR now, but.. seems not good to have wifi, mqtt, camera and qrcode all in the same task - would be better to make more threads...
2023-10-09 Kicad Schematic added, updated README
    [qrcode_BoM.ods, qrdoor.kicad_sch]
2024-01-01 bugfix in WifiMQTTManager, see README.md: Manager always killed all WiFi settings when not connecting to mqtt server. Now doing a reboot for retry.
    [qrdoor.ino]
2024-02-25 switched from ESPCAM to rpi pico with serial qrcode reader
2024-03-03 pcb layout made with blackboard PCB editor, source adapted to new pins
2024-03-03 new kicad schematic for the raspi pico
    [qrcode_BoM.ods, qrdoor.kicad_pcb, qrdoor.kicad_sch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]
2024-04-06 FreeCad model to park the hardware inside a mailbox slot
    [camera_cover-Körper.stl, camera_cover.FCStd, camera_cover_M6-Körper.stl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]
2024-04-06 updated Blackboard PCB layout with more clearance of the 5V power jumper
2024-04-06 bugfix try: MQTT check_msg caused an OSERROR: -1 try to fix it with modified uqmtt lib following https://github.com/micropython/micropython-lib/issues/363#issuecomment-774638386
    [main.py]
2024-04-27 changed to the umqtt library Version 2; reboot automatic when not seeing own topic echo seems to fix the hang up error
    [main.py]
2024-06-09 last circuitpython changes; smaller PCB holder
    [pcb_holder_small.FCStd]
